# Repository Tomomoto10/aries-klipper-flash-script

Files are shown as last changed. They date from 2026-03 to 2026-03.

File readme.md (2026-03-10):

<div align="center">

# **KLIPPER FOR THE VOXELAB ARIES 3D PRINTER** 

Run Klipper on a Raspberry Pi or Lunux device to control the Voxelab Aries
</div>

<p align="center">
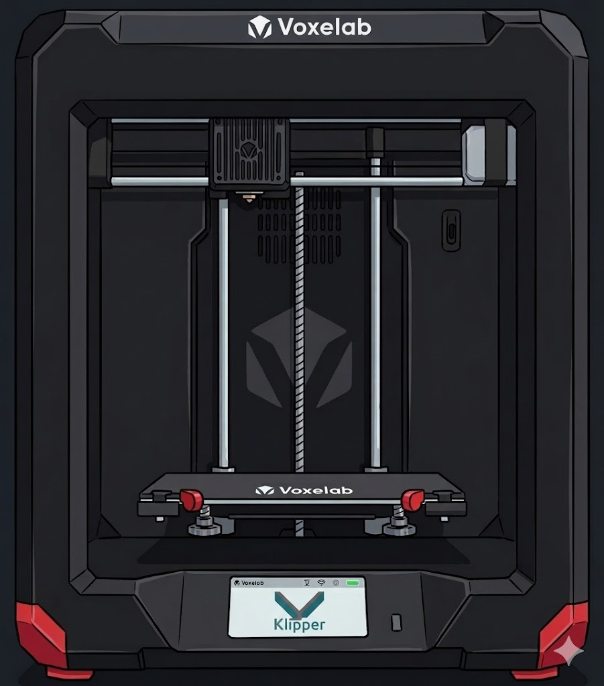
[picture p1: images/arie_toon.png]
.png broken.. woops
  
</p>

<div align="center">

**WORKING, BUT STILL IN PROGRESS**

Project fork of goopsie/aries-klipper-flash-script with extras from myself, other usefull sources are listed.

Added extra info for config changes, LEDS, MACROS, leveling, slicer profiles and more to come! 

**NOT COMPLETE, USE AT OWN RISK** 

</div>

## **CONTENTS**

[Pre-Install](#PRE-INSTALL)

[Install](#INSTALL)

[Post-Install](#POST-INSTALL)

  - [Bed-Leveling](#BED-LEVELING)

  - [Loading Filament](#LOADING-FILAMENT)

  - [Print Optimisation](#PRINT-OPTIMISATION)

  - [Slicer Profile](#SLICER-PROFILE)

  - [PID Calibration](#PID-CALIBRATION)

  - [Bed Probes](#BED-PROBES)

  - [Macros](#MACROS)

  - [LEDs](#LEDS)

  - [Fans](#FANS)

  - [Beeper](#BEEPER)

[Uninstall](#UNINSTALL)

[Credits and Contributions](#CREDITS-CONTRIBUTIONS)

### **PRE-INSTALL**
_________

- Install [SRECORD](https://srecord.sourceforge.net/), for converting klipper.bin file to work on the Voxelab (Works on Windows and Linux)

> *Windows: if installing srecord to a non-default directory, "to-hex.bat" will not work out of the box.

- Install Klipper host software to a Linux device of your choosing eg. Raspberry Pi.

> *[KIAUH](https://github.com/dw-0/kiauh) installer Recommended

- Connect printer to Klipper device via RX - TX pins on main board [Wiring Reference](images/wiring_reference.png)

 - Raspberry Pi: Wire Rx on Printer to Tx pin on Pi, Wire Tx on Printer to Rx pin on Pi 

 - USB Serial Converter: Wire Rx on Printer to Tx on Serial Adapter, Tx on Printer to Rx on Serial Adapter, no other pins needed.

 - Onboard ch340 Serial converter: Can be used by connecting usb cable to pins on [LCD Board](images/onboard_ch340-pinout.png)

- Format USB drive and Download this repo as .zip, extract all files to a USB drive, Make sure the usb drive shows up in your printer's menus before continuing.

### **INSTALL**
__________

- On klipper host run "make menuconfig" with settings as shown: [Make Settings](images/makemenuconfig-settings.png)

 - Serial Settings need to be adjusted according to connected device, see: [Serial Settings](images/makemenuconfig_serial.png)

> *(LCD) if using onboard ch340 Serial for usb connection
	
> *(PADS) if using rx-tx connections

 -If you cant get connection using "Internal Clock" for Clock Reference, you will need to use 12Mhz clock
  -Modify klipper/src/stm32/Kconfig with the following:

    #default 128000000 if MACH_N32G45x # old line
    default 144000000 if MACH_N32G45x  # new line

- Run "make" on klipper host

- Drag resulting klipper.bin onto root of USB drive.

- Convert klipper.bin to firmware.hex

> Windows: run "to-hex.bat" file also located on USB drive.
	
> Linux:  open terminal in root of USB drive, run: srec_cat klipper.bin -binary -offset 0x08000000 -output firmware.hex -Intel.

- You should see a new "firmware.hex" file was created on the USB drive.

- Turn off printer, if not off already. 

- Plug drive into printer, turn printer on.

 - You will see progress images come up on-screen, firmware.hex file will be automatically flashed to the mainboard via voxelab's built in programming tool.

 - On completion you will recieve a promt to connect your klipper host to the printer
	
 >  *Suggested you unplug the ribbon cable connecting the main board to the screen board as this cant be used anymore. 

 > *Screen can be removed and use KlipperScreen on Raspberry Pi Screen in place of original (Optional)
	
 > *Stock USB port can be re-wired to a usb plug and connected to Pi (Optional) [USB Pinout](images/front_usb_pinout.png)

- If using Raspberry Pi, you should already have rx-tx connected.

- If using other linux device, connect to printer via USB Serial Converter. 

- On another device, Open your chosen webUI (Fliudd/Mainsail) via the IP listed in the KIAUH UI during install, it wont have connection to your printer yet. 

 - Copy and replace the printer.cfg on the printer with the one in this repo using the web interface
	
- Restart Klipper
	
- Printer should now be connected to Klipper

**Follow steps below ONLY if your printer isnt automatically found* 

- You may need to update the printer.config with the serial port your printer is using:

On Klipper host, Run in terminal/ssh:

	ls /dev/serial/by-id/* 
	
- Change below in your printer.cfg, replace * with the device name show from command above 

	[mcu]
	serial: /dev/serial/by-id/*

- You should now have basic functionality of the printer, complete Leveling (Below) and any other optional extra steps to get extra functiality before printing for the first time.

### **POST-INSTALL**
___________

### **CONFIG-CHECKS**

- The printer should work fine after installing. If you are worried or feel the need you can run [Configuration Checks](https://www.klipper3d.org/Config_checks.html?h=pid#configuration-checks) to ensure all sensors and motors are working correctly. 

### **CALIBRATE-PID**

- On the Web interface (Fluidd/Mainsail) run boh Hotend and Heatbed PID calibrations to ensure precise heating.

Hotend Calibration:

 - Run the PID_EXTRUDER Macro, wait till finished and klipper will restart

Hotbed Calibration: 

 - Run the PID_BED Macro, wait till finished and klipper will restart

### **BED-LEVELING**

- Use the front bed screws to make any adjustments to pre level the bed as best as possible, have the front slightely lower than the rear if possible.
  *In WebUI Settings, Invert the Z-Axis Controls so that + goes up and - goes down 

- Use the Klipper [Manual Leveling](https://www.klipper3d.org/Manual_Level.html#manual-leveling) guide for detailed instructions.

 *Procedure is: 0: Rear Stationary Screw, 1: Left Adjustable Screw, 2: Right Adjustable Screw

**Adjust Rear Stationary Screw Z-Height**

- In the Fluidd/Mainsail webUI:

 - Press the HOME ALL Axis Button and wait for printer to Home and lift the bed up to the nozzle. 

 - Press REAR_SCREW button in the Macro window to move nozzle over rear screw. 

  >  *adjust z -xis towards the nozzle small amounts at time (0.00 SHOULD be nozzle directly on the bed), I ended up with 0.35 z offset for example

 -Run the following Macro in the webUI and follow the [Paper Leveling](https://www.klipper3d.org/Bed_Level.html#the-paper-test) procedure:

 	REAR_SCREW_Z_ADJUST

 - 'ACCEPT' the changes once satisfied and klipper will restart 

**Adjust Front Screw Z-Heights**

- On the Fluidd/mainsail webUI command terminal:

> *As the front of bed is floating and unsupported, Try not to put pressure on the bed while adjusting and taking measure with the paper as this will dramatically affect the bed height.

 - Run the following, then follow [Paper Leveling](https://www.klipper3d.org/Bed_Level.html#the-paper-test) procedure for the 2 front screws:

 > *'ACCEPT' and skip 'Screw 1' as this screw can not be adjusted. 

 	BED_SCREWS_ADJUST 

 - For the first adjustment of the front screws press 'Adjusted' after adjusting to move to the next. After re-adjusting a second time, press 'ACCEPT' for each.

 - Klipper will save changes and restart

### **LOADING FILAMENT**

- Load Filament into Extruder unit on back of printer
 - On Mainsail/Klipper WebUi Press LOAD_FILAMENT on the Macro panel
  -Extruder will heat up and filament will be fed through extruder. 

- To Unload, press UNLOAD_FILAMENT on the Macro panel. This will heat the extruder and pull the filament back out of the extruder. 

### **PRINT OPTIMISATION**

- To get the best quality prints out of your machine, follow the [Resonance Compensation](https://github.com/Klipper3d/klipper/blob/master/docs/Resonance_Compensation.md) and [Pressure Advance](https://www.klipper3d.org/Pressure_Advance.html#pressure-advance) guides. 

- Other guides like [Excluding Objects](https://www.klipper3d.org/Exclude_Object.html#exclude-objects) can add extra controls, find more features and controls under the sidebar of the linked page.  

### **SLICER PROFILE**

- Included in the repo is an ORCA SLICER .3mf project (orca_slicer_profile_xyz.3mf)

- Also has XYZ Calibration Cube for [Print Optimisation](#PRINT-OPTIMISATION)

 - Import this into Orca Slicer (File->Open Project

 - Save the Aries Profile and Print Settings by editing the names and saving each as a 'User Preset', then remove the "Project Preset".
   
   -See screenshots in folder for info

- Currently only 1 available and tested profile that has basic SAFE settings for 0.4mm Nozzle and PLA Filament.

- More to come! Submissions welcome! 

### **BED-PROBES**

**(NOT TESTED)**

- BL touch or other clones can be plugged directly into the hotend board via the 5 pin socket 
- Useful for for Bed Mesh Probing and Z-Axis Homing

 - [Hotend Board Pinout](images/hotend_pinout.png)
 
 - [Probe Pinouts](images/probe_pinout.png)

- The below lines are the mapped pins for the hotend board, Copy into your printer.config
	[bltouch]
	sensor_pin: ^PB1
	control_pin: PB0

- Follow [BLTouch](https://www.klipper3d.org/BLTouch.html#bl-touch) to set up BL Touch sensor with your printer

> *Other sensors can be used but are WIP and not covered in this guide yet.

### **MACROS**

- Macros in the provided printer.config will provide basic functionality. To gain further control, you can add your own macros to gain extra control. 

> *Additional macros will be added in the future, any submissions are welcome. 

### **LEDS** 

Hotend LED

- Hotend LED can be set to default OFF, and turned on only when printing.

 - Either during [makemenuconfig](images/makemenuconfig-settings.png) remove the '!PC1' (Highlighted) and leave blank

 - Or if you have already configured with this setting, in printer.cfg change: "[led extruder_led] white_pin:" to !PC1
 
 - You can modify/extend the gcode your printer.cfg to play different tones (r2-d2, example coming)

 - Add the following to your Slicer Start_Gcode to turn on at print start (You could use a custom START_PRINT Gcode instead to streamline this)  

	;start gcode
	SET_LED LED=extruder_led White=1.0 

RGB
- You can add additional ARGB leds eg. for chassis lighting 

 - See [Wiring Reference](images/wiring_reference.png) for pads on the mainboard.

  - Solder the "Data" line from the ARGB led strip to r99 on the Aries mainboard 

  - Solder 5v and Ground wires from ARGB led strip to LCD connector pins (or other 5v/Gnd source)

- The following lines in your printer.cfg adjust the control, adjust 'initial' values as needed for the led color when when turning on printer. 

	[neopixel chassis_lights]
	pin: PA15
	chain_count: 1   # NUMBER_OF_LEDS_HERE
	color_order: GRB # depends on strip
	initial_RED: 1   # if you want
	initial_GREEN: 1 # if you want
	initial_BLUE: 1  # if you want

- Led brightness and Color can now be adjusted in your chosen interface (Fluidd/Mainsail/KlipperScreen)

### **FANS**

**(UNTESTED)**

- Unused fan PA3 in printer.cfg is: [FAN1] on the printer mainboard

- Can be used to add a additional FAN OR BEEPER to the printer

- Modify printer.cfg as per [Fans](https://www.klipper3d.org/Config_Reference.html?h=fan#fans)

- To gain control of the fan, eg. when hotend is on:
	
	[controller_fan mcu_fan1]
	pin: PA3
	max_power: 0.75
	heater: extruder

### **BEEPER**
- To add beeper to get feedback from your printer follow [This Guide](https://ellis3dp.com/Print-Tuning-Guide/articles/useful_macros/beeper.html).
  
- Change pin to PA3 and and add macro to printer.cfg

- Once added you can add the macro into your slicer settings to get audible feedback (start print, end print etc.)

- Use the beeper for fancy sounds, heres some [Configs](https://github.com/majarspeed/Profiles-Gcode-Macros/tree/main/Beeper%20tunes) by @majarspeed with some great tunes!
  *UNTESTED, as my beeper is ony single tone. Will Update when new Piezo arrives. 

### **UNINSTALL**
_____

- Reverting to stock firmware is simple, just follow steps below

 - Un-solder uart pins from Mainboard, plug back in screen cables and any others you may have unplugged

 - Turn the printer as normal.

 - You'll get a [Prompt on-screen](images/update_failed.png), stating "The firmware failed to update. Press OK to retry", with an "OK" button.

 - Once you press the button, the LCD board will flash the original firmware to the Mainboard, 

 - You can now use the printer as normal.

### **CREDITS-CONTRIBUTIONS**
__________

Couldnt have done without: Original project owner, infinte help on reddit.

 @GOOPSIE (Git) OopsieGoopsie (Reddit)

  https://github.com/goopsie/aries-klipper-flash-script

  https://www.reddit.com/r/VoxelabAries/comments/1lna0p0/got_klipper_flashed_to_my_aries/
___________________

Bed Leveling Macros and Configs.

 @LaszloLitaus_2081172 (Printables.com) 

  https://www.printables.com/model/881037-voxelab-aries-converter-plates/files

______________

Beeper Configs 

@ellis3dp

 https://ellis3dp.com/Print-Tuning-Guide/articles/useful_macros/beeper.html

____________________

Beeper Tunes 

 @majarspeed

 https://github.com/majarspeed/Profiles-Gcode-Macros/tree/main/Beeper%20tunes

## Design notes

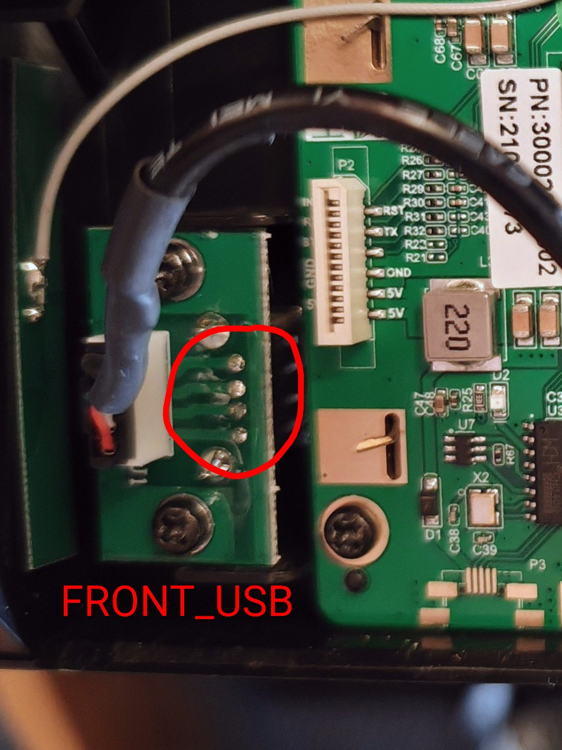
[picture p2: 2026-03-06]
images/front_usb_pinout.png

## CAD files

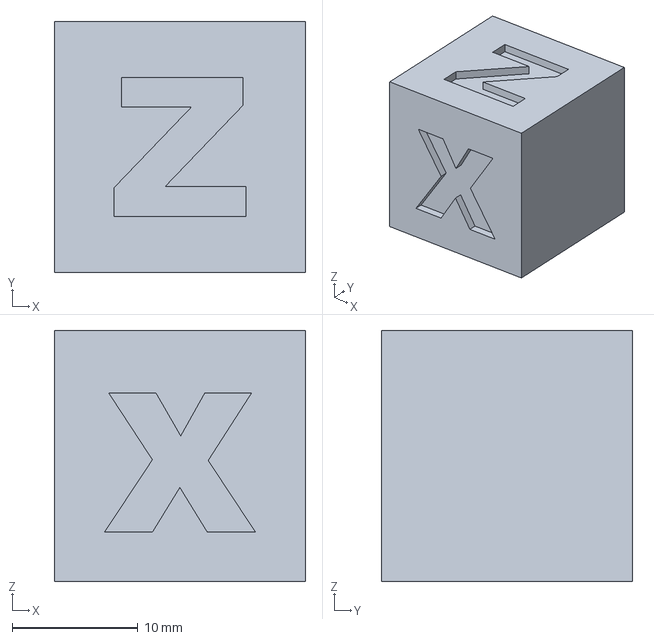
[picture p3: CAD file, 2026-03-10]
orca_slicer_profile_aries.3mf
20.0 x 20.0 x 20.0 mm

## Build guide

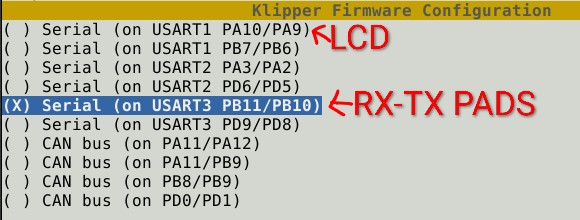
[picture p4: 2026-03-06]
images/makemenuconfig_serial.png

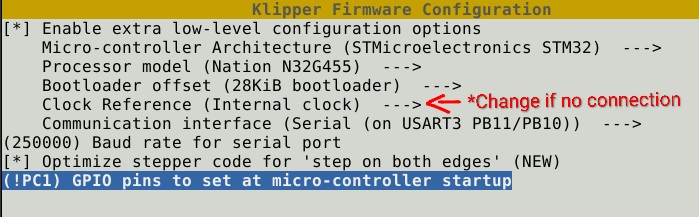
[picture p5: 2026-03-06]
images/makemenuconfig-settings.png

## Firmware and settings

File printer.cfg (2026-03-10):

[include fluidd.cfg]

[mcu]
serial: /dev/ttyUSB0
restart_method: command
 
[printer]
kinematics: cartesian
max_velocity: 1000
max_accel: 7000
max_z_velocity: 30
max_z_accel: 100
 
[force_move]
enable_force_move: true
 
[virtual_sdcard]
path: ~/printer_data/gcodes
 
[stepper_x]
step_pin: PB8
dir_pin: PB7
enable_pin: !PC13
microsteps: 16
rotation_distance: 34
endstop_pin: !PC15
position_endstop: 205.5
position_max: 205.5
homing_speed: 100
second_homing_speed: 5
 
[stepper_y]
step_pin: PB6
dir_pin: PB5
enable_pin: !PC13
microsteps: 16
rotation_distance: 34
endstop_pin: !PA6
position_max: 205.5
position_endstop: 205.5
homing_speed: 100
second_homing_speed: 5
 
[stepper_z]
step_pin: PB4
dir_pin: PB3
enable_pin: !PC13
microsteps: 16
rotation_distance: 8
endstop_pin: !PA7
#position_endstop: 216.3 #Default 216.5
position_max: 216.5 #Default 216.5
homing_speed: 25
second_homing_speed: 5
 
[input_shaper]
shaper_freq_x: 46.43  # frequency for the X mark of the test model
shaper_freq_y: 35.71  # frequency for the Y mark of the test model
shaper_type: mzv

[homing_override]
axes: z
set_position_z: 0
gcode:
    G90                # Use absolute positioning
    G1 Z10 F600        # Lift Z to 10mm (safer to move XY)
    G28 X Y            # Home X and Y
    G1 X115 Y100 F3000 # Move to middle of bed
    G28 Z              # Home Z
    G1 Z10 F600        # Lift Z after homing to 0

[bed_screws]
screw1: 115, 170
screw2: 43, 25
screw3: 188, 25 

[extruder]
step_pin: PC14
dir_pin: PB9
enable_pin: !PC13
microsteps: 16
rotation_distance: 32.5
nozzle_diameter: 0.400
filament_diameter: 1.75
heater_pin: PA1
sensor_type: EPCOS 100K B57560G104F
sensor_pin: PA4
#control: pid
#pid_Kp: 29.460
#pid_Ki: 2.067
#pid_Kd: 104.952
min_temp: 0
max_temp: 250
min_extrude_temp: 150
max_extrude_only_distance: 500
max_extrude_cross_section: 2.0
 
[heater_bed]
heater_pin: PA2
sensor_type: EPCOS 100K B57560G104F
sensor_pin: PA5
control: pid
pid_Kp: 57.069
pid_Ki: 1.469
pid_Kd: 554.286
min_temp: 0
max_temp: 110

[filament_switch_sensor runout_sensor]
pause_on_runout: True
debounce_delay: 1
switch_pin: PC0

[fan]
pin: PC2
max_power: 0.75
 
[heater_fan heatbreak_cooling_fan]
pin: PC3
heater: extruder
fan_speed: 1.0
 
[led extruder_led]
white_pin: PC1

[controller_fan mcu_fan1]
pin: PA0
max_power: 0.75
stepper: stepper_x, stepper_y, stepper_z
heater: heater_bed, extruder

#unused fan FAN1 pin is PA3


[output_pin beeper]
pin: PA3
value: 0
shutdown_value: 0

#######MACROS##########

[exclude_object]

[display_status]

[gcode_macro CANCEL_PRINT]
description: Cancel the actual running print
rename_existing: CANCEL_PRINT_BASE
gcode:
  TURN_OFF_HEATERS
  CANCEL_PRINT_BASE
  G90 
  SET_KINEMATIC_POSITION Z=0 
  G0 Z10 F600 ; Z Changes lift height'
  G1 X205 Y205 F1000 ; Move to Safe Zone
  M84
  
 
[pause_resume]
 
[gcode_macro PAUSE]
description: Pause the actual running print
rename_existing: PAUSE_BASE
# change this if you need more or less extrusion
variable_extrude: 1.0
gcode:
  ##### read E from pause macro #####
  {% set E = printer["gcode_macro PAUSE"].extrude|float %}
  ##### set park positon for x and y #####
  # default is your max posion from your printer.cfg
  {% set x_park = printer.toolhead.axis_maximum.x|float - 5.0 %}
  {% set y_park = printer.toolhead.axis_maximum.y|float - 5.0 %}
  ##### calculate save lift position #####
  {% set max_z = printer.toolhead.axis_maximum.z|float %}
  {% set act_z = printer.toolhead.position.z|float %}
  {% if act_z < (max_z - 2.0) %}
      {% set z_safe = 2.0 %}
  {% else %}
      {% set z_safe = max_z - act_z %}
  {% endif %}
  ##### end of definitions #####
  PAUSE_BASE
  G91
  {% if printer.extruder.can_extrude|lower == 'true' %}
    G1 E-{E} F2100
  {% else %}
    {action_respond_info("Extruder not hot enough")}
  {% endif %}
  {% if "xyz" in printer.toolhead.homed_axes %}
    G1 Z{z_safe} F900
    G90
    G1 X{x_park} Y{y_park} F6000
  {% else %}
    {action_respond_info("Printer not homed")}
  {% endif %} 
 

[gcode_macro RESUME]
description: Resume the actual running print
rename_existing: RESUME_BASE
gcode:
  ##### read E from pause macro #####
  {% set E = printer["gcode_macro PAUSE"].extrude|float %}
  #### get VELOCITY parameter if specified ####
  {% if 'VELOCITY' in params|upper %}
    {% set get_params = ('VELOCITY=' + params.VELOCITY)  %}
  {%else %}
    {% set get_params = "" %}
  {% endif %}
  ##### end of definitions #####
  {% if printer.extruder.can_extrude|lower == 'true' %}
    G91
    G1 E{E} F2100
  {% else %}
    {action_respond_info("Extruder not hot enough")}
  {% endif %}  
  RESUME_BASE {get_params}


[gcode_macro LOAD_FILAMENT]
variable_load_distance: 425
variable_purge_distance: 150
gcode:
 SET_LED LED=extruder_led White=1.0 
 G1 z50 F500 #Lower hotbed
 G1 XG1 X180 F3000.0 #Move to purge position
 {% set speed = params.SPEED|default(300) %}
 {% set max_velocity = printer.configfile.settings['extruder'].max_extrude_only_velocity * 100%}
 {% set EXTRUDER_TEMP = params.EXTRUDER_TEMP|default(230)|float %}
 SAVE_GCODE_STATE NAME=load_state
 #M300 #Beep
 G91 #Set incremental move mode
 G92 E0 #Reset extruder to position zero
 #Display message
 M117 Heating...
 M109 S{EXTRUDER_TEMP} #Heat hot end to 230 as default
 #M300 #Beep
 #Display message
 M117 Loading filament...
 G1 E{load_distance} F{max_velocity} #Fast load filament
 G1 E{purge_distance} F{speed} #Slow load filament
 #M300 #Beep
 #Display message
 M117 Filament loaded
 M109 S{0} #Turn off heat 
 RESTORE_GCODE_STATE NAME=load_state 



[gcode_macro UNLOAD_FILAMENT]
variable_unload_distance: 470
gcode:
 SET_LED LED=extruder_led White=1.0 
 G1 XG1 X180 F3000.0 #Move to purge position
 G1 z50 F500 #Lower hotbed
 {% set speed = params.SPEED|default(300) %}
 {% set max_velocity = printer.configfile.settings['extruder'].max_extrude_only_velocity * 100%}
 {% set EXTRUDER_TEMP = params.EXTRUDER_TEMP|default(230)|float %}
 SAVE_GCODE_STATE NAME=unload_state
 #M300 #Beep
 G91 #Set incremental move mode
 G92 E0 #Reset extruder to position zero
 #Display message
 M117 Heating...
 M109 S{EXTRUDER_TEMP} #Heat hot end to 230 as default
 #M300 #Beep
 #Display message
 M117 Unloading filament...
 G0 E10 F300 #Exrtude some filament
 G0 E5 F3600 #Push back filament to minimize stringing
 G0 E-15 F3600 #Quickly move filament in the cold zone
 G0 E-20 F300 #Continue extraction slowly to allow filament to cool
 G1 E-{unload_distance} F{max_velocity} #Fast unload
 #M300 #Beep
 #Display message
 M117 Filament unloaded
 M109 S{0} #Turn off heat
 RESTORE_GCODE_STATE NAME=unload_state


[gcode_macro REAR_SCREW_Z_ADJUST]
gcode:
 G90
 G28 ;Home All Axis
 G1 Z5 F300 ;Move Z up 
 G0 X115 Y170 G3600
 Z_ENDSTOP_CALIBRATE
 SAVE_CONFIG

[gcode_macro BED_SCREW_Z_ADJUST]
gcode:
 G90
 G28 ;Home All Axis
 G1 Z5 F300 ;Move Z up 
 BED_SCREWS_ADJUST 
 SAVE_CONFIG


[gcode_macro UNSAFE_RAISE_TOOL] 
#Raise the toolhead without homing 
gcode:
 G90 
 SET_KINEMATIC_POSITION Z=0 
 G0 Z10 F600 ; Z Changes lift height
 M84


[gcode_macro PID_EXTRUDER]
gcode:
 PID_CALIBRATE HEATER=extruder TARGET=210
 SAVE_CONFIG

[gcode_macro PID_BED]
gcode:
  PID_CALIBRATE HEATER=heater_bed TARGET=60
  SAVE_CONFIG



#*# <---------------------- SAVE_CONFIG ---------------------->
#*# DO NOT EDIT THIS BLOCK OR BELOW. The contents are auto-generated.
#*#
#*# [stepper_z]
#*# position_endstop = 215.950
#*#
#*# [extruder]
#*# control = pid
#*# pid_kp = 26.646
#*# pid_ki = 1.630
#*# pid_kd = 108.915

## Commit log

2026-03-03 Revise README for clarity and additional instructions
    Updated README to clarify installation instructions and add details about macros, leveling, and LED configurations.
2026-03-03 Update printer configuration with new settings and macros
    [printer.cfg]
2026-03-03 Fix typos and clarify printer.cfg instructions
    Updated instructions for printer configuration and macros.
2026-03-06 Re write printer.cfg and update settings
    complete Rehaul of printer config, still WIP
    [printer.cfg]
2026-03-06 Add images Klipper installation
2026-03-06 Update printer configuration with new settings
    [printer.cfg]
2026-03-06 Revise readme for Klipper installation instructions
    Updated readme with additional information on installation, configuration, and usage of Klipper for the Voxelab Aries 3D printer.
2026-03-06 Delete Orca Slicer Profile directory
    Not Working will re-upload
    [Aries-PLA.3mf]
2026-03-06 Update printer configuration settings
    [printer.cfg]
2026-03-06 Update printer configuration file
    [printer.cfg]
2026-03-07 Working Orca Slicer Profile
    start gcode with purge line at front of bed
    [orca_slicer_profile_xyz.3mf]
2026-03-07 NEW - Macro Leveling and PID calibration
    Updated calibration instructions and added details about macros for saving configurations.
2026-03-09 Update unused fan configuration from PA0 to PA3
2026-03-09 Add printer configuration settings to printer.cfg
    [printer.cfg]
2026-03-09 Update printer configuration with correct PINs
    PA0 / PA3 swapped
    Changed fan speeds to fix PID Issue
    [printer.cfg]
